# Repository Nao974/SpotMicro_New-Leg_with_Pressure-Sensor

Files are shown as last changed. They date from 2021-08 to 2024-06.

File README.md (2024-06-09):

# SpotMicro: New leg with pressure sensor

[Version française](./README_FR.md)

This project aims to add pressure sensors to the end of each leg of the SpotMicro in order to know :
- If it touches the ground (boolean True / False)
- The force exerted on each of them
- And at a time "t" the direction of the force exerted (pressure // release)

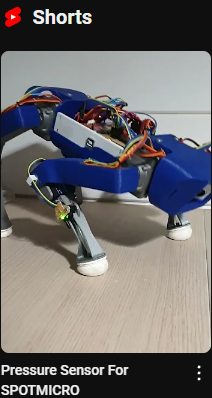
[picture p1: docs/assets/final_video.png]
Video Presentation (https://youtube.com/shorts/aT10lHqLCCs)


## Summary

- ### [The genesis of the project and the functional specifications](./docs/GENESIS_EN.md)
- ### [The Making](./docs/MAKING_EN.md)
- ### [The Programming](./docs/CODING_EN.md)

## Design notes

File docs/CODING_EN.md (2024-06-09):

# Programming
The examples given use the libraries of the [Choreograph](https://github.com/Nao974/choreograph-git) project for the management of movements and servomotors. I let you take a look at this related project.

Libraries for the management of servos not documented in this project:
- lib/choreograph
- lib/Oscillator
- lib/Servo

## LegPressureSensor Library

Written for VSCode, just copy it into the *./lib* folder of your Plateform-IO project.

### Constants

```C
const uint16_t CALIBRATE_NB = 100;
const float CALIBRATE_STANDARD_DEVIATION = 350.0;
const uint8_t TRIGGER_PRESSURE = 10;
const uint8_t TRIGGER_DIRECTION = 5;
```

- CALIBRATE_NB: Number of measurements when calculating the calibration value
- CALIBRATE_STANDARD_DEVIATION: Standard deviation used in calculating the normalization coefficient
- TRIGGER_PRESSURE: Deviation from the calibration validating a change of state.
- TRIGGER_PRESSURE: Deviation from the calibration validating a change of direction.

### Public Methods (functions)

```C
void init(const uint8_t pinPC, const uint8_t pinLed);  // Initialization
        
void calibrateLow(); // Calculation of the calibration in the air  
uint16_t calibrateLowValue(); // Return the calculated released pressure     
void calibrateLowWrite(uint16_t value); // Set value released pressure
        
void calibrateHigh(); // Calculation of the calibration press max         
uint16_t calibrateHighValue(); // Return the calculated released pressure      
void calibrateHighWrite(uint16_t value); // Set value max pressure

void calculateNormalizeFactor(); // Calculation of the normalization factor  
float normalizeFactorValue(); // Return the calculated released pressure                
void normalizeFactorWrite(float value); // Set Ratio Calibration

void read(); // Pressure reading and state update
void readNz(); // Pressure reading, NormaliZation and state update

int16_t pressureValue(); // Return the last measured pressure      
int16_t pressureValueNz(); // Return the last measured pressure normalized

int16_t pressureMax(); // Return the current max pressure
int16_t pressureMaxNz(); // Return the current max pressure normalized

int8_t direction(); // Return the direction of movement      
bool isPressed(); // Returns True / False if pressed

void stateReset(); // Reset state at Release
```

### Declaration and Initialization
Following the example of the program *1xleg_FrontLeft.cpp*

- Declaration of an array of type LegPressureSensor for the 4 legs
```C
LegPressureSensor legs[4];
```

- Initialization of the 4 legs with the analog input pin for reading the sensor and the digital output for the LED:
```C
legs[LEG_FL].init(A8, 13);
legs[LEG_BL].init(A9, 12);
legs[LEG_FR].init(A10, 11);
legs[LEG_BR].init(A11, 10);
```

### Calibration
The robot must be placed on a support with the legs not touching the ground:  
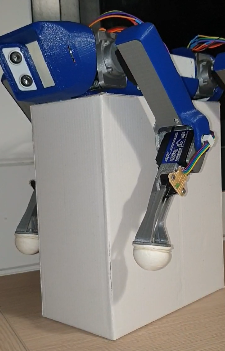
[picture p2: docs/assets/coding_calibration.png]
Robot on support


**The calibration must be done *empty* then by compressing the pad**

- Calibration *empty* for the 4 legs:  
```C
for ( uint8_t leg = 0; leg < 4; leg++)
    legs[leg].calibrateLow();
```

- Then calibration with max pressure:
```C
for ( uint8_t leg = 0; leg < 4; leg++) {
    legs[leg].calibrateHigh();
    legs[leg].calculateNormalizeFactor();
}
```

For each leg one after the other, the LED will flash to indicate the leg being calibrated, it is advisable at this time to press the pad several times in order to have the maximum pressure value. Once the measurement is done, the program moves on to the next leg by flashing its LED.

The calibration does not have to be done at each start, you can save the result in non-volatile memory with the function:
```C
epromSave(legs);
```

Then during the following starts, reload the previous calibration:
```C
epromLoad(legs);
```C

The constant allows you to launch or not the calibration:
```C
#define CALIBRATE false
```

## Example Source Code

- **pressureSensorVumetreUno.cpp**: Allows you to test the tab made with visual feedback on an 8 LED vumeter. Assembly made on an Arduino Uno board, it is necessary to modify the environment in *platformio.ini*  
[Youtube video](https://youtu.be/5eInNg3Okts)

- **1xLeg_FrontLeft.cpp**: When pressing on the pad, the leg retracts, it returns to its initial position once the pad is released  
[Youtube video](https://youtube.com/shorts/aT10lHqLCCs)

- **cushion.cpp**: Cushioning of the front legs when it falls or when a blow to the head causes pressure on the front sensors:  
[Youtube video t=9s](https://www.youtube.com/shorts/aT10lHqLCCs?t=9)

---

[back to menu](../README.md)

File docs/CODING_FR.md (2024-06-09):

# Programmation
Les exemples donnés utilisent les librairies du projet [Choreograph](https://github.com/Nao974/choreograph-git) pour la gestion des mouvements et des servomoteurs. Je vous laisse prendre connaissance de ce projet connexe.

Librairies pour la gestion des servos non documentées dans ce projet :
- lib/choreograph
- lib/Oscillator
- lib/Servo

## Librairie LegPressureSensor

Ecrite pour VSCode il suffit de la copier dans le dossier *./lib* de votre projet Plateform-IO.

### Les Constantes

```C
const uint16_t CALIBRATE_NB = 100;
const float CALIBRATE_STANDARD_DEVIATION = 350.0;
const uint8_t TRIGGER_PRESSURE = 10;
const uint8_t TRIGGER_DIRECTION = 5;
```

- CALIBRATE_NB : Nombre de mesure lors du calcul de la valeur de calibration
- CALIBRATE_STANDARD_DEVIATION: Ecart type utilisé dans le calcul du coefficient de normalisation
- TRIGGER_PRESSURE : Ecart par rapport à la calibration validant un changement d'état.
- TRIGGER_PRESSURE : Ecart par rapport à la calibration validant un changement de sens.

### Les Méthodes Publics (fonctions)

```C
void init(const uint8_t pinPC, const uint8_t pinLed);  // Initialization
        
void calibrateLow(); // Calculation of the calibration in the air  
uint16_t calibrateLowValue(); // Return the calculated released pressure     
void calibrateLowWrite(uint16_t value); // Set value released pressure
        
void calibrateHigh(); // Calculation of the calibration press max         
uint16_t calibrateHighValue(); // Return the calculated released pressure      
void calibrateHighWrite(uint16_t value); // Set value max pressure

void calculateNormalizeFactor(); // Calculation of the normalization factor  
float normalizeFactorValue(); // Return the calculated released pressure                
void normalizeFactorWrite(float value); // Set Ratio Calibration

void read(); // Pressure reading and state update
void readNz(); // Pressure reading, NormaliZation and state update

int16_t pressureValue(); // Return the last measured pressure      
int16_t pressureValueNz(); // Return the last measured pressure normalized

int16_t pressureMax(); // Return the current max pressure
int16_t pressureMaxNz(); // Return the current max pressure normalized

int8_t direction(); // Return the direction of movement      
bool isPressed(); // Returns True / False if pressed

void stateReset(); // Reset state at Release
```

### Déclaration et Initialisation
Suivant l'exemple du programme *1xleg_FrontLeft.cpp*

- Déclaration d'un tableau de type LegPressureSensor pour les 4 pattes  
```C
LegPressureSensor legs[4];
```

- Initialisation des 4 pattes avec la broche d'entrée analogique pour la lecture du capteur et la sortie digitale pour la LED :    
```C
legs[LEG_FL].init(A8, 13);
legs[LEG_BL].init(A9, 12);
legs[LEG_FR].init(A10, 11);
legs[LEG_BR].init(A11, 10);
```

### Calibration
Le robot doit être placé sur un support avec les pattes qui ne touchent pas le sol :  
Robot sur support

**La calibration doit se faire *à vide* puis par compression du coussinet**

- Calibration *à vide* pour les 4 pattes :  
```C
for ( uint8_t leg = 0; leg < 4; leg++)
    legs[leg].calibrateLow();
```

- Puis calibration avec pression max :  
```C
for ( uint8_t leg = 0; leg < 4; leg++) {
    legs[leg].calibrateHigh();
    legs[leg].calculateNormalizeFactor();
}
```
Pour chaque patte l'une après l'autre, la LED va clignotée afin d'indiquer la patte en cours de calibration, il convient à ce moment de presser plusieurs fois le coussinet afin d'avoir la valeur max de pression. Une fois la mesure effectuée, le programme passe à la patte suivante en faisant clignoter sa LED.

La calibration n'est pas à faire à chaque démarrage, vous pouvez sauvegarder le résultat en mémoire non volatile avec la fonction :  
```C
epromSave(legs);
```

Puis lors des démarrages suivant, recharger la calibration précédente :  
```C
epromLoad(legs);
```C

La constante permet de lancer ou non la calibration :  
```C
#define CALIBRATE false
```

## Code Source Exemple

- **pressureSensorVumetreUno.cpp** : Permet de tester la patte réalisée avec un retour visuel sur un vumètre à 8 LEDs. Montage réalisé sur une carte Arduino Uno, il convient de modifier l'environnement  dans *platformio.ini*  
[Vidéo Youtube](https://youtu.be/5eInNg3Okts)

- **1xLeg_FrontLeft.cpp** : Lors de l'appui sur le coussinet, la patte se rétracte, elle reprend sa position initiale une fois le coussinet relaché  
[Vidéo Youtube](https://youtu.be/5eInNg3Okts)

- **cushion.cpp** : Amortissement des pattes avant quand il tombe ou lors d'un coup sur la tête provoquant une pression sur les capteurs avants :   
[Vidéo Youtube t=9s](https://youtu.be/5eInNg3Okts)

---

[retour au menu](../README_FR.md)

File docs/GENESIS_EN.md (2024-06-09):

# Project genesis

The realization of a proof of concept (POC) around the MPU6050 gyroscope-accelerometer, highlights a problem of application of the attitude compensation coefficient which can cause the leg to lose contact with the ground and lead to a loss of stability:

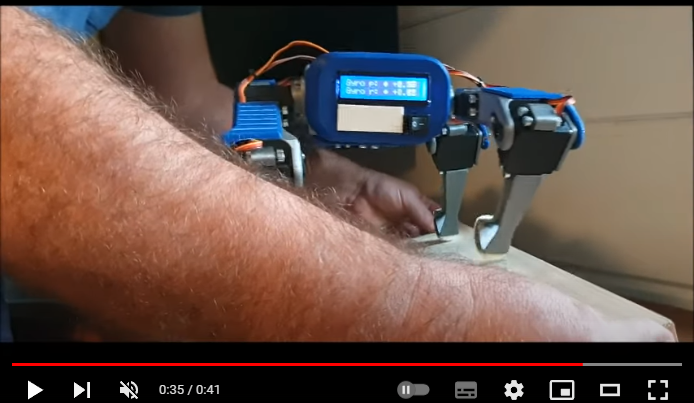
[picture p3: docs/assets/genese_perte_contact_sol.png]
Gyro (https://youtu.be/NudqEaxzqT8?t=35)


Beyond knowing if a leg touches the ground, it would also be interesting to know the pressure exerted on each of them in order to adapt the robot's movements, for example to cushion a fall.

## Functional specifications

- **SF01- For each leg, is it resting on the ground?**

Whatever the pressure exerted on the leg, a variable will indicate by Yes / No if pressure is exerted on it.

- **SF02- For each leg, what is the pressure exerted on it?**

The value of the measured pressure will be a real number, standardized so that the measurements on the 4 legs are comparable on a common scale.

- **SF03- For each leg, what is the direction of the force exerted?**

Depending on the pressure exerted at time T compared to the pressure at T-1, a variable will indicate by Pressed // Released the direction of the force exerted.

## Research and study of existing sensors
The measuring system must be robust and precise, hermetic to dust and gravel.

- Bending sensors
    - These sensors are fragile and deform over time
    - A mechanism to apply force to the sensor will not be hermetic and will not cover the entire point of contact between the leg and the ground

- By Hall effect
    - The idea is to place iron dust in a flexible part at the end of the leg and measure the deformation by a Hall effect sensor
    - The manufacturing of this part will not be standard for each leg
    - The signal will be too complex to analyze for a µController

- By air pressure
    - Like Unitree, create a flexible "pear" and measure the air flow generated by its deformation
    - Totally hermetic
    - Effective regardless of the point and pressure angle
    - Simple signal to process

### Creation of the "Pear"

Like the leg of the Unitree A1 robot, I started to create a flexible "Pear".

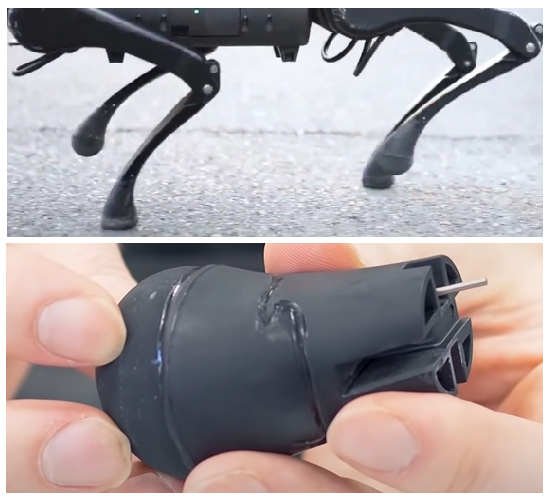
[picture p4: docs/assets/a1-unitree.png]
a1-unitree


First by 3D printing in **FLEX** filament (TPU), but the exercise is not easy because it is flexible (yes indeed!!!) and it is difficult to have a constant flow at the extruder outlet.
After testing different thicknesses, it remains too rigid and tears very quickly:

TPU test (https://youtu.be/ME4x9cBKyLQ?si=gAKe6t903O2WUMFG)

I have not tested the TPE filament which is even more flexible because the experience with FLEX was already complicated.

---

### New Option: **Silicone**

The principle is to print 3D molds in order to "model" Silicone bathroom joints:

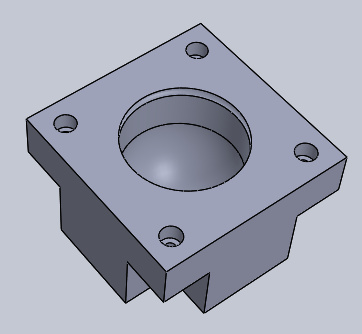
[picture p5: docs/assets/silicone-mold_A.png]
silicone-mold-A
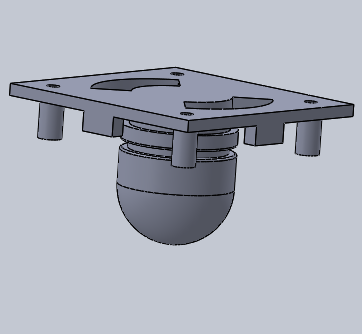
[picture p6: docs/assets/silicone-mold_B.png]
silicone-mold-B
<div align="center">&nbsp;</div>

The Silicone is first kneaded in water saturated with dishwashing liquid:

Silicone Mold (https://youtu.be/2pnlD2yrzPs)

A few hours of drying and here is our part ready, several Tests thickness have been made:

Result Silicone Mold (https://youtu.be/qxboo4HXB_k)

---

### The air pressure sensor

Having no idea of the pressure differential in the "pear" between a pressed or released state, I tested 2 sensors with different precision.

I chose analog sensors because all the I2C found had a fixed address, therefore incompatible with the SportMicro which has 4 legs, therefore 4 pressure sensors.

#### **MPX4250AP**
With a precision of 20 mV/kPa, this sensor is not sensitive enough, even when I blow into it at maximum, the value varies only very slightly.

#### **MPX5010DP**
With an accuracy of 450mv/kPa, this sensor is great, I capture light pressures as well as heavy crushing:

Result Sensor (https://youtu.be/x-UZMXbWamg)

[DataSheet MPX5010DP](../assets/datasheets/mpx5010-2165.pdf)

## Concept validation

The creation of a silicone pad coupled to the MPX5010DP pressure sensor is validated by the creation of the following prototype:

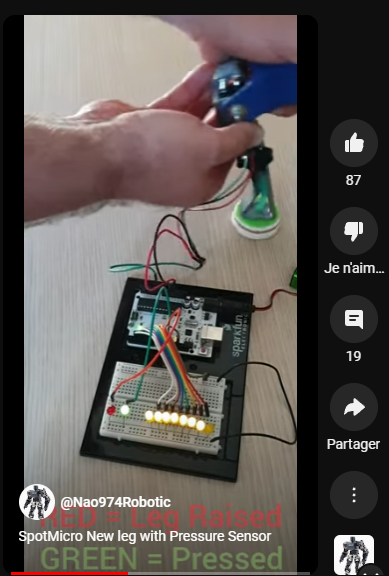
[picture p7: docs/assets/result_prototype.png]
Video Test Result (https://youtu.be/5eInNg3Okts)


---

[back to menu](../README.md)

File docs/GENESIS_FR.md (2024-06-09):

# Genèse du projet

La réalisation d'une preuve de concept (POC) autour du gyroscope-accéléromètre MPU6050, met en évidence un problème d'application de coefficient de compensation de l'assiette qui peut faire perdre le contact de la patte avec le sol et entrainer une perte de stabilité :

Gyro (https://youtu.be/NudqEaxzqT8?t=35)

Au-delà de connaitre si une patte touche le sol, il serait également intéressant de connaitre la pression exercée sur chacune d'elle afin d'adapter les mouvements du robot, par exemple amortir une chute.

## Spécifications fonctionnelles

- **SF01- Pour chaque patte, est-elle en appui sur le sol ?**

Quelle que soit la pression exercée sur la patte, une variable indiquera par Oui / Non si une pression est exercée sur celle-ci.

- **SF02- Pour chaque patte, quelle est la pression exercée sur celle-ci ?**

La valeur de la pression mesurée sera un nombre réel, standardisé afin que les mesures sur les 4 pattes soient comparables sur une échelle commune.

- **SF03- Pour chaque patte, quelle est la direction de la force exercée ?**

Suivant la pression exercée au moment T en comparaison de la pression à T-1, une variable indiquera par Pressée // Relâchée la direction de la force exercée.

## Recherche et étude des capteurs existants
Le système de mesure doit être robuste et précis, hermétique à la poussière et aux gravillons.

-	Les capteurs de flexion
    - Ces capteurs sont fragiles et se déforment à la longue
    - Un mécanisme afin d'appliquer la force sur le capteur ne sera pas hermétique et ne permettra pas de couvrir la totalité du point de contact entre la patte et le sol

-	Par effet hall
    - L'idée est de placer de la poussière de fer dans une pièce flexible au bout de la patte et de mesurer la déformer par un capteur à effet hall
    - La fabrication de cette pièce ne sera pas standard pour chaque patte
    - Le signal sera trop complexe à analyser pour un µControleur

-	Par pression d’air
    - A l'image d'Unitree, créer une "poire" flexible et mesurer le flux d'air généré par sa déformation
    - Totalement hermétique
    - Efficace quel que soit le point et l'angle de pression
    - Signal simple à traiter

### Création de la "Poire"

A l'image de la patte du robot A1 d'Unitree, je suis partie sur la création d'une "Poire" flexible.

a1-unitree

D'abord par impression 3d en filament **FLEX** (TPU), mais l'exercice n'est pas facile car celui est flexible (ben oui !!!) et il est difficile d'avoir un débit constant à la sortie de l'extrudeur.
Après des tests de différentes épaisseurs, cela reste trop rigide est ce déchire très rapidement :

Test TPU (https://youtu.be/ME4x9cBKyLQ?si=gAKe6t903O2WUMFG)

Je n'ai pas testé le filament TPE qui est encore plus souple car l'expérience avec le FLEX était déjà compliquée.

---

### Nouvelle Option : **le Silicone**

Le principe est d'imprimer des moules en 3D afin de "modeler" du Silicone de joints de salle de bain :

<div align="center">silicone-mold-A&nbsp;silicone-mold-B</div>  

Le Silicone est au préalable malaxé dans de l'eau saturé en liquide vaisselle :

Silicone Mold (https://youtu.be/2pnlD2yrzPs)

Quelques heures de séchage et voilà notre pièce est prête, plusieurs Tests d'épaisseur ont été réalisé :

Result Silicone Mold (https://youtu.be/qxboo4HXB_k)

---

### Le capteur de pression d'air

N'ayant aucune idée du différentiel de pression dans la "poire" entre un état pressé ou relâché, j'ai testé 2 capteurs avec un précision différente.

J'ai choisi des capteurs analogiques car l'ensemble des I2C trouvés avaient une adresse fixe, donc incompatible avec le SportMicro qui a 4 pattes, donc 4 capteurs de pression.

#### **MPX4250AP**
Avec une précision de 20 mV/kPa, ce capteur n'est pas assez sensible, même quand je souffle dedans au maximum, la valeur ne varie que très légèrement.

#### **MPX5010DP**
Avec une précision de 450mv/kPa, ce capteur est super, je capte les légères pressions ainsi que les gros écrasements :

Result Sensor (https://youtu.be/x-UZMXbWamg)

[DataSheet MPX5010DP](../assets/datasheets/mpx5010-2165.pdf)

## Validation du concept

La création de coussinet en silicone couplet au capteur de pression MPX5010DP est validé par la création du prototype suivant :

Video Résultat Test (https://youtu.be/5eInNg3Okts)

---

[retour au menu](../README_FR.md)

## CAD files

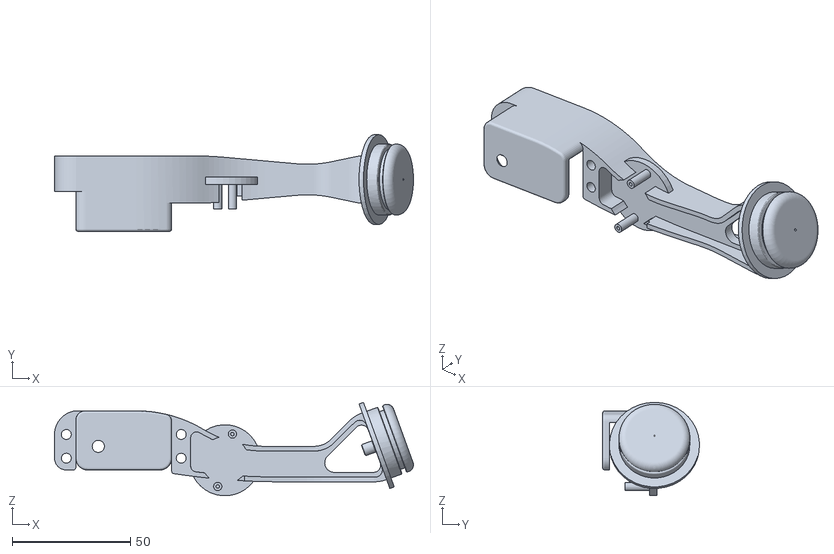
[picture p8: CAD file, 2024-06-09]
assets/MCAD/L_wrist_mg_pressure.STL
151.6 x 40.9 x 39.4

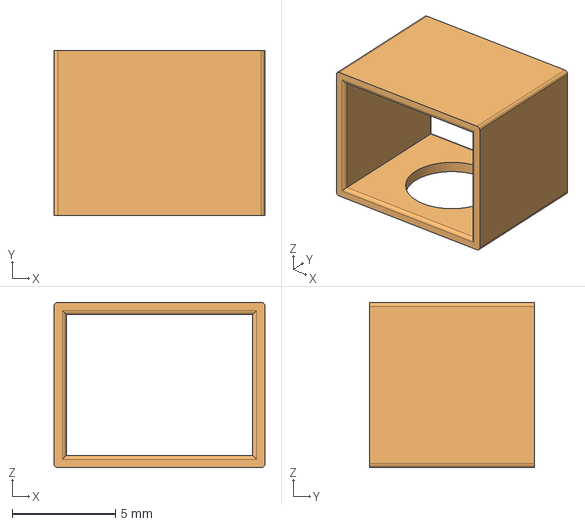
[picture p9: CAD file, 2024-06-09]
assets/MCAD/wire_pass_elbow.FCStd
10.2 x 8.00 x 8.00 mm

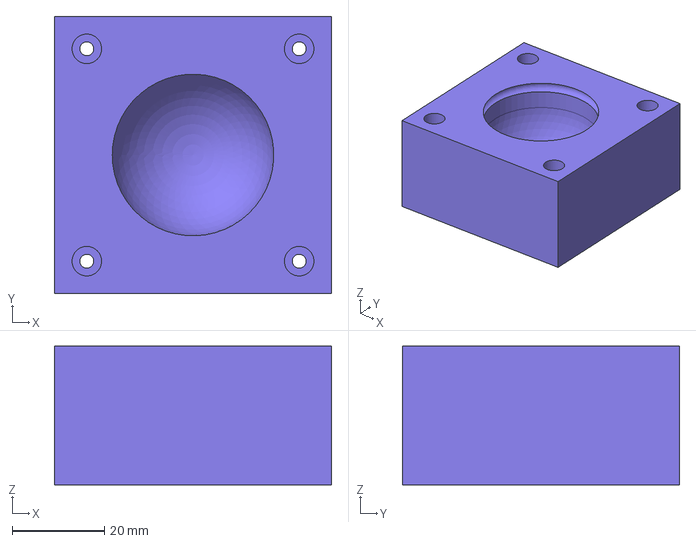
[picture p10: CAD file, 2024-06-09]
assets/MCAD/Silicone-Mold_v4-A_35mm.FCStd
60.0 x 60.0 x 30.0 mm

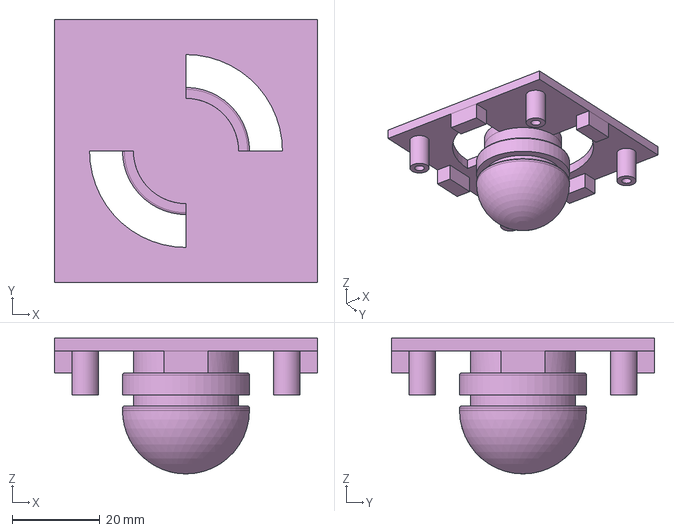
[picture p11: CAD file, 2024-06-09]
assets/MCAD/Silicone-Mold_v4-B_29mm.FCStd
60.0 x 60.0 x 31.0 mm

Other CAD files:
assets/MCAD/Silicone-Mold_v4-A_35mm.stl
assets/MCAD/Silicone-Mold_v4-B_29mm.stl
assets/MCAD/wire_pass_elbow.stl

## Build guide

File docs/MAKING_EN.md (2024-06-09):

# Manufacturing

There are 3 steps to make a leg with a pressure sensor:

- Printing the modified leg
- Manufacturing the "pads"
- Mini electronic card & wiring

## Modified leg
You will find in the *MCAD* folder the file *L_wrist_mg_pressure.STL* corresponding to the modified leg on the left side. A symmetry from your Slicer will allow you to have the leg on the right side.

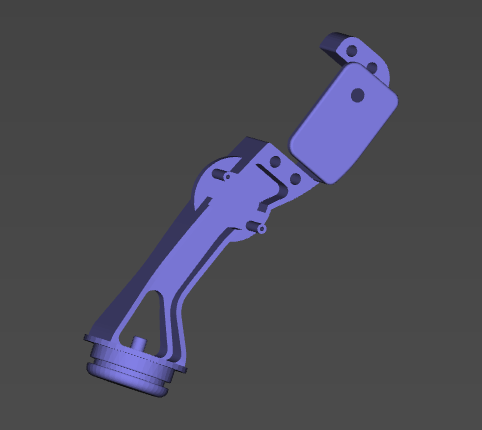
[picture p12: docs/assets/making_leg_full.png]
Piece Leg


- The end has been modified to accommodate the pad.
A "nipple" has been added for the connection to the pressure sensor by a flexible tube of XXX mm diameter.  
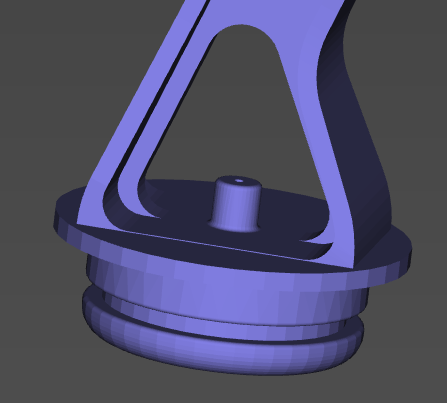
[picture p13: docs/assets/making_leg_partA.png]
Leg end
  

- A support by the sensor PCB has been added:  
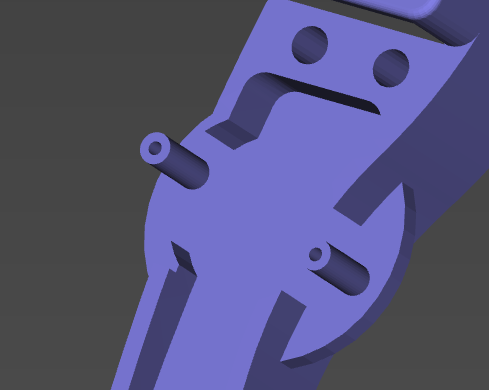
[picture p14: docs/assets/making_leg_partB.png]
Support PCB


- Finally, it is necessary to add a flexible tube with an internal diameter of 4mm and a length of 55 mm. I found some in a pet store for aquarium air pumps.  
Tube

## Making the "cushion"

The principle is to print 3D molds in order to "model" Silicone bathroom joints:

<div align="center">silicone-mold-A&nbsp;silicone-mold-B</div>

- The Silicone is first kneaded in water saturated with dishwashing liquid:  
Silicone Mold (https://youtu.be/2pnlD2yrzPs)

- A few hours drying and here is our part ready, several thickness tests have been carried out, for this it is enough to modify the diameter of the ball of the mold B:  
Result Silicone Mold (https://youtu.be/qxboo4HXB_k)

- RAS on the assembly side, it is enough to add a tight elastic:  
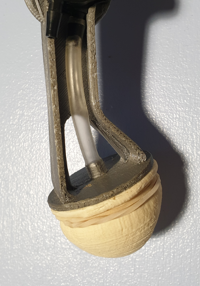
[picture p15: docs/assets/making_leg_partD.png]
Assembly with Elastisque


### Mini electronic card & wiring
#### Sensor side card
A 1st card is installed on each leg in order to connect the pressure sensor to the µController:
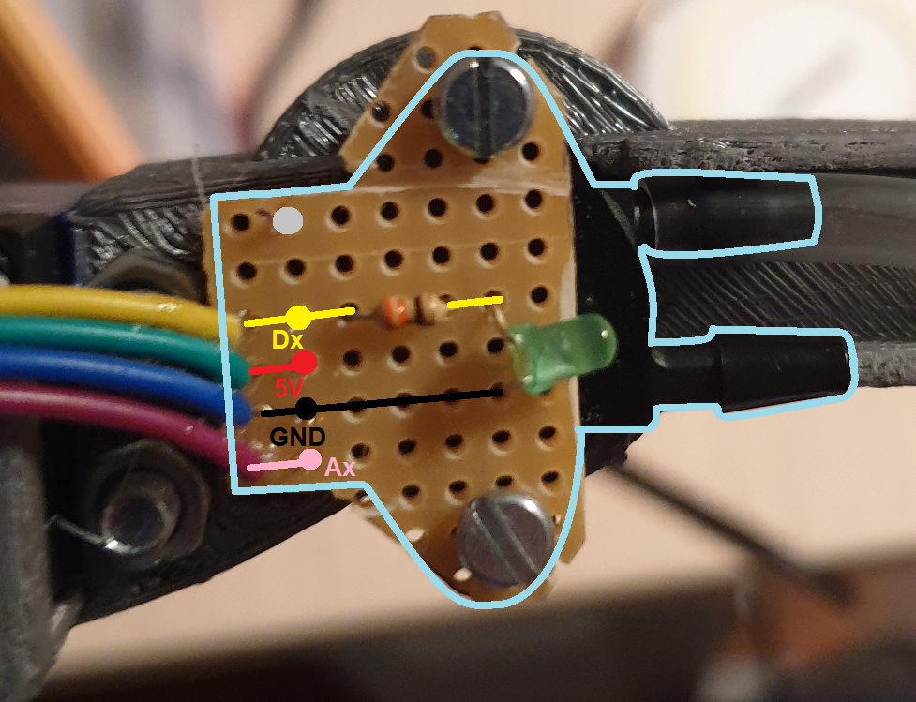
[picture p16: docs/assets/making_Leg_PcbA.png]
PCB Leg


List of components:
- 1x Sensor mpx5010-2165
- 1x Led
- 1x 220 ohm resistor

Wiring:
- The 1 V OUT pin of the sensor will be connected to an analog input Ax of the µController
- The resistor will be connected to a digital output of the µController Dx allowing the LED to be lit.

#### µController side card
Shield type card to add to the Arduino Mega allowing to transmit the 5V power supply, the ground, the signal to light the LED, and to retrieve the value of the sensor:
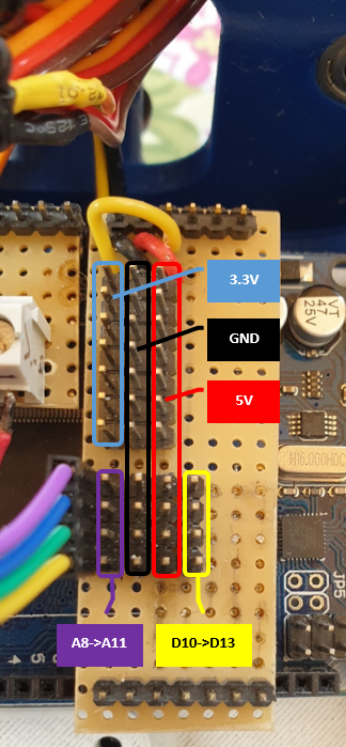
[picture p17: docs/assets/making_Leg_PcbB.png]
PCB Shield µC


#### Grommet
I modeled a grommet to add on the "elbow" of the leg that you will find in the *MCAD* folder:
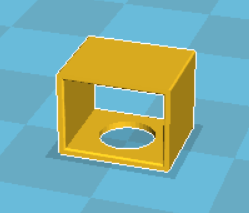
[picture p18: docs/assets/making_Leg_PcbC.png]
Wire Grommet Modeling
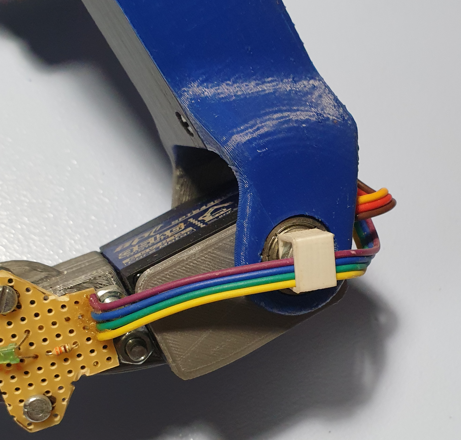
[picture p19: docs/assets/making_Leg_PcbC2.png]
Mounted Wire Grommet
<div align="center">&nbsp;</div>

---

[back to menu](../README.md)

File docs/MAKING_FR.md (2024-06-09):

# La Fabrication

Il y 3 étapes afin de réaliser une patte avec capteur de pression :

- Impression de la patte modifiée
- Fabrication des "coussinet"
- Mini carte électronique & câblage

## Patte modifiée
Vous trouverez dans le dossier *MCAD* le fichier *L_wrist_mg_pressure.STL* correspondant à la patte modifiée côté gauche. Une symétrie depuis votre Slicer vous permettra d'avoir la patte coté droit.

<div align="center">Piece Patte</div>

- Le bout a été modifié afin d'accueillir le coussinet.
Une "tétine" a été ajouté pour la liaison au capteur de pression par un tube flexible de XXX mm de diamètre.  
Bout patte

- Un support par le PCB du capteur a été ajouté :  
Support PCB

- Pour finir, il convient de rajouter un tube flexible d'un diamètre interne de 4mm et d'une longueur de 55 mm. J'en ai trouvé dans une animalerie pour les pompes à air d'aquarium.  
Tube

## Fabrication des "coussinet"

Le principe est d'imprimer des moules en 3D afin de "modeler" du Silicone de joints de salle de bain :

<div align="center">silicone-mold-A&nbsp;silicone-mold-B</div>  

- Le Silicone est au préalable malaxé dans de l'eau saturé en liquide vaisselle :  
Silicone Mold (https://youtu.be/2pnlD2yrzPs)

- Quelques heures de séchage et voilà notre pièce est prête, plusieurs Tests d'épaisseur ont été réalisé, pour cela il suffit de modifier le diamètre de la boule du moule B :  
Result Silicone Mold (https://youtu.be/qxboo4HXB_k)

- RAS coté montage, il suffit de rajouter un élastique bien serré :  
Montage avec Elastisque

### Mini carte électronique & câblage
#### Carte coté capteur
Une 1ere carte est installée sur chaque patte afin de relier le capteur de pression au µControleur :  
<div align="center">PCB Patte</div>

Liste des composants :  
- 1x Capteur mpx5010-2165
- 1x Led
- 1x résistance 220 ohms

Câblage :  
- La patte 1 V OUT du capteur sera reliée à une entrée analogique Ax du µControleur
- La résistance sera reliée à une sortie digitale du µControleur Dx permettant d'allumer la LED.

#### Carte coté µControleur
Carte de type Shield à rajouter sur l'Arduino Mega permettant de transmettre l'alimentation 5V, la masse, le signal pour allumer la LED, et récupérer la valeur du capteur:  
<div align="center">PCB Shield µC</div> 

#### Passe-fil
J'ai modélisé un passe-fil à rajouter sur le "coude" de la patte que vous retrouverez dans le dossier *MCAD* : 
<div align="center">Modélisation Passe Fil&nbsp;Passe Fil monté</div>  

---

[retour au menu](../README_FR.md)

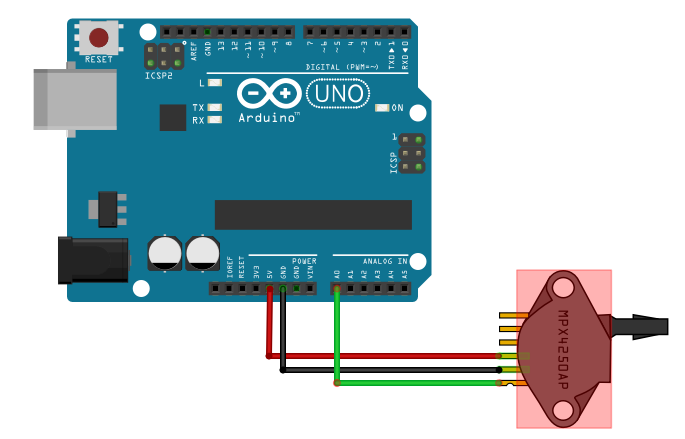
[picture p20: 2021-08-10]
docs/assets/wiring.png

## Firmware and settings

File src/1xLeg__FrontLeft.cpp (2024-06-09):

#include <Arduino.h>
#include <spotMicro.h>
#include <LegPressureSensor.h> 
#include <SpotEprom.h>

#include <Servo.h>
#include <Oscillator.h>
#include <choreograph.h>

/* You can see the result here :

************
Please, go see my Choreogrpah Software repository 
for details on movement management
https://github.com/Nao974/choreograph-git
*/

#define CALIBRATE false

LegPressureSensor legs[4];

const uint16_t TIME = 150; // Home to Down in 1000 ms
const uint16_t FRAME = 10; // Time divider to limit steps every x ms

// Variable for movements
float decrement[NBRE_SERVO];
uint16_t iteration;
int8_t direction;
uint32_t next_time;

void setup() {
    // Init each pressure sensor 
    legs[LEG_FL].init(A8, 13);
    legs[LEG_BL].init(A9, 12);
    legs[LEG_FR].init(A10, 11);
    legs[LEG_BR].init(A11, 10);

    #if CALIBRATE == true 
        for ( uint8_t leg = 0; leg < 4; leg++)
            legs[leg].calibrateLow();

        for ( uint8_t leg = 0; leg < 4; leg++) {
            legs[leg].calibrateHigh();
            legs[leg].calculateNormalizeFactor();
            Serial.print("Leg "); Serial.print(leg); Serial.print(": ");
            Serial.print("Min "); Serial.print(legs[leg].calibrateLowValue());Serial.print(" => ");
            Serial.print("Max "); Serial.print(legs[leg].calibrateHighValue());Serial.print(" => ");
            Serial.print("Fact Nz "); Serial.println(legs[leg].normalizeFactorValue());
        }    
        Serial.println("Backup Calibration");
        epromSave(legs);
    #else
        // Load calibrate and normalized coeff for each pressure sensor 
        epromLoad(legs);
    #endif

    for (uint8_t servo=0; servo<NBRE_SERVO; servo++) {
        // initialization of each servo and movement to the initial position
        chore.servoInit(pin[servo]);
        chore.servoOffset(servo, offset[servo]);
        moveSingle_safe(servo, BASE_HOME[servo]); 
        pos_actuelle[servo] = BASE_HOME[servo];

        // Calculates the difference between the 2 positions for each servo 
        decrement[servo] = double(TETE_BASSE[servo] - BASE_HOME[servo]) / (TIME / FRAME);
    }

    iteration = 0;  
    direction = 0;  
    next_time = millis();
}

void loop() {
    // Pressure reading and status update
    legs[LEG_FL].readNz();

    if (millis() >= next_time){
        if ( legs[LEG_FL].isPressed() ) direction = 1;
        else direction = -1;

        // Limitation to not exceed the min / max positions
        if ( ( (iteration + direction) < (TIME / FRAME) ) && ( (iteration + direction) >= 0) ) iteration += direction;

        // Displacement of each servo of LEG_FL according to calculated iteration
        for (uint8_t i=0; i< 3; i++)
            moveSingle_safe(i, BASE_HOME[i] + ( decrement[i] * iteration) );
        next_time = millis() + FRAME; // every FRAME ms
    }
    
   delay(50);
}

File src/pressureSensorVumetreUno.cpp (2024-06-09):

#include <Arduino.h>
#include <LegPressureSensor.h> 

/*  You can see the result here :
 https://youtube.com/shorts/5eInNg3Okts?si=phbLiTOYaWVGga2u
*/

// Pin of the differents leds On Arduino Uno
const uint8_t pin_vumetre[]={2,3,4,5,6,7,8,9};
const uint8_t pin_pressed = 10;
const uint8_t pin_released = 11;
const uint8_t pin_leg = 13;

// Variable for the Vumeter display
int16_t vumetre = 0;
uint8_t led = 0;

//Declaration of a 1st leg
LegPressureSensor leg1;

void setup() {
    // Initialize the Leg with the corresponding pins
    leg1.init(A0, pin_leg);
    // Release calibration of the leg
    delay(500);
    leg1.calibrateLow();
    leg1.calibrateHigh();
    leg1.calculateNormalizeFactor(); 

    // Initializes pins for Leds
    for (uint8_t i =0; i<8; i++) {
        pinMode(pin_vumetre[i], OUTPUT);
        digitalWrite(pin_vumetre[i], HIGH);
    }    
    pinMode(pin_pressed, OUTPUT);
        digitalWrite(pin_pressed, HIGH);
    pinMode(pin_released, OUTPUT);
        digitalWrite(pin_released, HIGH);
}

void loop() {
    // Pressure reading and status update
    leg1.readNz();

    // LED management according to status
    digitalWrite(pin_released, !leg1.isPressed());
    digitalWrite(pin_pressed, leg1.isPressed());
    
    //VU-meter update
    if ( vumetre > (led*32) && leg1.isPressed() ) digitalWrite(pin_vumetre[led], HIGH);
    else digitalWrite(pin_vumetre[led], LOW);
    // Once the last LED has been processed, a new value is displayed
    if ( led >= 7 ) {
        led=0;
        vumetre = leg1.pressureValueNz();
    }
    // Otherwise processing of the next led
    else led++;  
}

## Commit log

2021-08-10 Add Wiring in Readme
2021-08-28 Add molding video in Readme
2024-05-19 Leds in common +5V
2024-06-09 full update
    [L_wrist_mg_pressure.STL, Leg-End_v3b_34mm.STL, Silicone-Mold_A_v3_35mm.STL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]
